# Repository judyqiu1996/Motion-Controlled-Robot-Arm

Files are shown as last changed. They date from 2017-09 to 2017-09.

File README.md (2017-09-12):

# Motion Controlled Robot Arm

1. Designed a circuit and PCB board receiving the sensor information from arm by Bluetooth and controlling the action of the robot.

2. Used I2C and SPI methods to communicate between chip and software.

3. Devised an algorithm of filtering and processing sensor data, manipulating robot arm in 3 Axis, including pitch and roll axes.

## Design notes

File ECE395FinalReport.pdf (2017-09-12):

# Motion Controlled Robotic Arm

# ECE 395 Spring 2017 Project

# Sanchit Anand & Yujia Qiu

# Introduction

For our project in ECE 395, we decided to make a motion controlled robotic arm that is capable of detecting the orientation of a person’s hand, and attempting to replicate the motion. Our project was based on another project from the Fall of 2013 - Human Controlled Robotic Arm and Legs Movement, and we attempted to extend the degrees of motion of the arm.

At the end of the project, major changes were made to the motion filtering algorithms, to support a new system of kinematics. This report is written in the hope that future students will be able to expand upon our work.

# Schematic

The schematic files we used include a different version of the LPC ARM processor, with almost identical functionality.

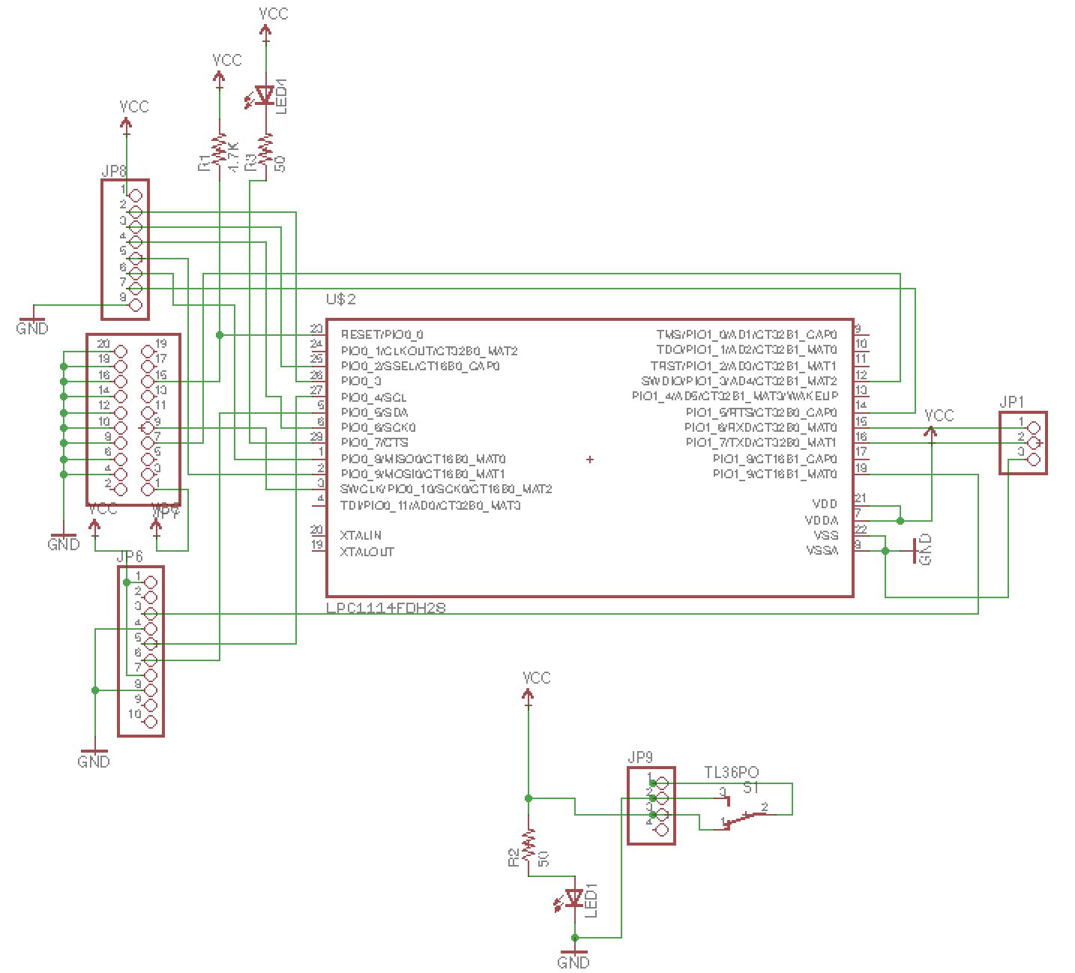
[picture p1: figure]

# Figure: Schematic Diagram

The 8 pins jumper is to connect the bluetooth breakout, the 10 pins jumper is to connect sensor breakout. The 20 pins jumper is to connect JTAG. The “JP1” is for switch which controls the power on or off. The “JP9” is connect to the power cell.

# PCB

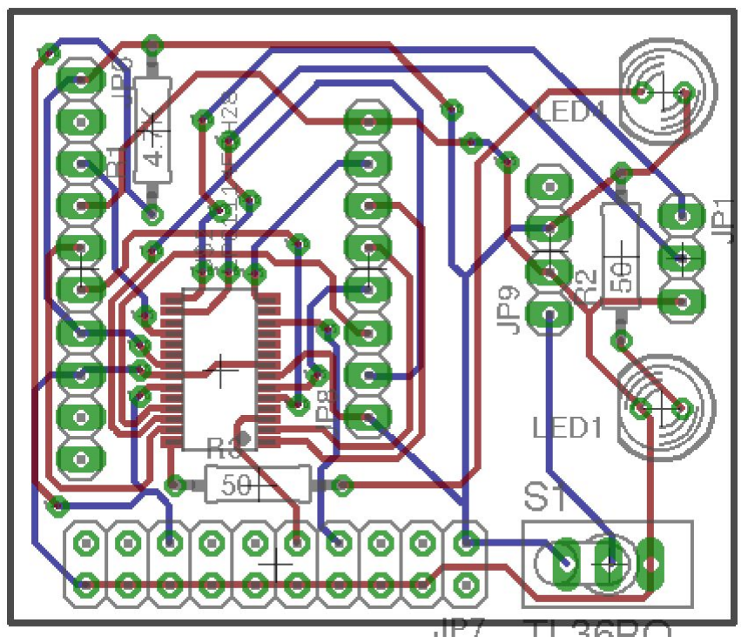
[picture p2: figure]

# Figure: PCB

# This brd file is transferred from schematic. And the figure below is the

actual picture of the pcb board.

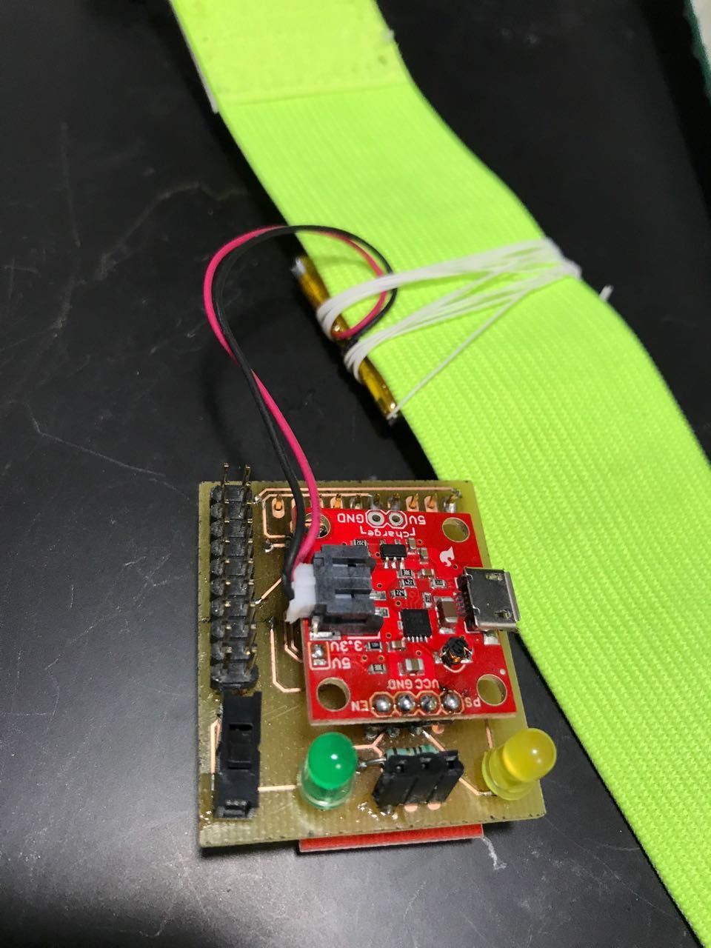
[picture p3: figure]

# Figure: pcb board picture

# Operation

The project hardware is split up between two different boards. There is a main prototype board

# that controls the motors, via USART protocol. This main board contains a bluetooth

module(NRF24l01+) that polls for data from the motion pads at regular intervals. This angular data is transformed into motor values, and transmitted via USART. There is an LED attached for debugging purposes, as well as connections for downloading code via JTAG module.

The motion pads consist of an battery pack, connected to a power chip that regulates voltage at 3.3V. It also contains a six axis IMU unit, the MPU-6050, for taking measurements of motion along the pitch and roll axes. The microprocessor performs complementary filtering on the data. Finally the bluetooth module (NRF24l01+), transmits the pitch and roll angles to the main board.

There are 4 motion pads in total, one for each shoulder joint, and one for each elbow joint. The 2 shoulder pads measure angles along pitch and roll axes, and transmit to the main board. Then the two separate motors in the shoulder joint get actuated by their respective angle. The 2 elbow pads measure motion along the pitch direction and transmit it to the main board, where the pitch angle from the shoulder joint is subtracted from it. The elbow motor is actuated by the resulting angle.

A short diagram is presented below to help understand the different angles used.

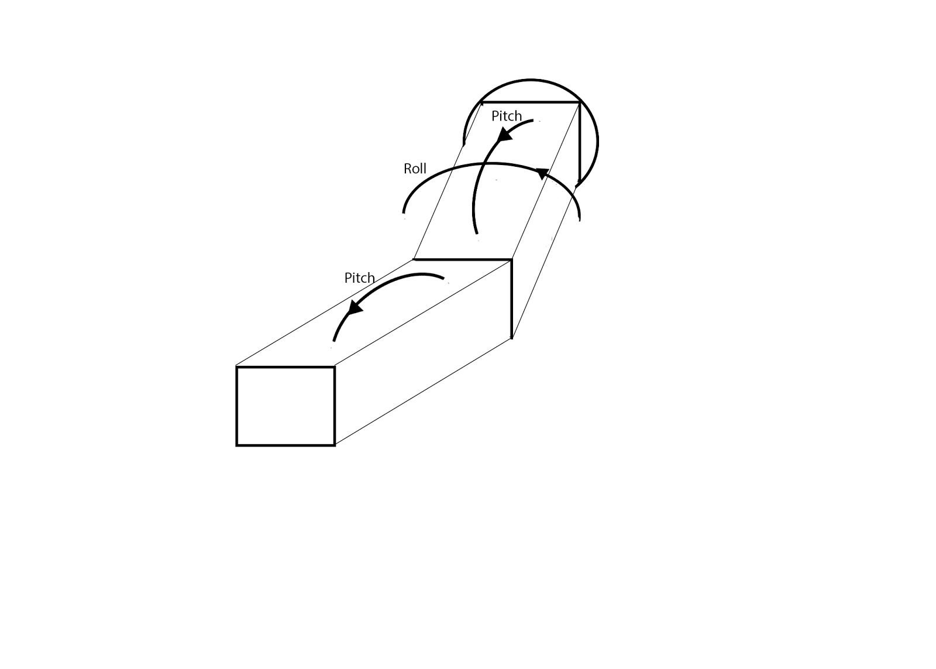
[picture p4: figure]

# Conclusion

The project yielded satisfactory results as determined by us. Lots of improvements can still be made on it. First of all, by using a 9 degree of freedom IMU, instead of a 6 degree of freedom IMU (The MPU-6050 used for this project), one would be able to measure all 3 axes of motion, instead of just two, and with a higher precision as well. One of the main limitations of using just 6 degrees of freedom is that the error in angles increases as the combined pitch and roll angles

# get higher. Secondly, by learning how to use the inbuild proprietary DMP software on the

MPU-6050, one would be able to offload all the filtering onto the IMU itself, and obtain much more accurate data in the process.

Finally, We found that the servos used in this project were liable to decreased performance after operating for some time. We are unsure whether it is the result of wear and tear, whether it is a fundamental property of the specific brand we used or an issue with the code being used. In either case, it is recommended that more research is done while selecting and using servos and motors to use in future projects.

# Appendix : Hardware

# NXP LPC1114 Cortex M0 Microprocessor (x5) The processors that perform all of the filtering and calculations, as well as

communications with various peripheral devices.

# http://www.nxp.com/documents/data_sheet/LPC111X.pdf

MPU6050 6-Axis Accelerometer/Gyroscope These are the main sensors. The inbuilt gyroscope and accelerometers measures the orientation of the board with respect to gravity. These measurements are stored in registers of the chip, and can be accessed by microprocessors via I2C protocol. The communication rate is 100Kbits/s. Documentation for this chip is available at http://www.invensense.com/mems/gyro/mpu6050.html

# NRF24L01+ Transceiver

This is a 2.4Ghz radio frequency transmitter/receiver. It is present on both the satellite and the main board, providing a form of wireless communication between the boards.

# The transceiver operates in two modes, one for receiving (RX) and one for transmission (TX). This can be configured by commands from the microprocessor through Serial

Peripheral Interface (SPI) protocol.

# http://www.nordicsemi.com/eng/Products/2.4GHz-RF/nRF24L01

Dynamixel AX-12a Servos The AX12 servos are the actuators of the robot, serving as rotational joints based on the commands sent by the microprocessor. These servos work on 9-12V power source and communicate with the microprocessor via a single line. The ID of the servos determines which servo along the series line to receive the instruction as passed from the

processor. The servos utilize half-duplex communication protocol.

# http://www.crustcrawler.com/products/bioloid/docs/AX-12.pdf

# Appendix : Code

complementary.c : C file containing the majority of filtering code.

#include "complementary.h"

float x_filter=0, y_filter=0, z_filter=0, angle_x=0, angle_y=0, angle_z=0 ;
float pitch , yaw, roll ;
float sign;
void complementary_filter(float * Buf,float accel_x, float accel_y, float accel_z, float gyro_x, float gyro_y, float gyro_z,float dt)
{

x_filter = 0.9*x_filter + 0.1*accel_x;
z_filter = 0.9*z_filter + 0.1*accel_z;
y_filter = 0.9*y_filter + 0.1*accel_y;
//acc_angle_y = atan2(x_filter, -z_filter) * 180/3.14159265358979323 ; //angle_y = 0.98*(gyro_y*dt + angle_y) + 0.02*acc_angle_y;

//acc_angle_x = atan2(y_filter, -z_filter) * 180/3.14159265358979323 ; //angle_x = 0.98*(gyro_x*dt + angle_x) + 0.02*acc_angle_x;

//acc_angle_z = atan2(x_filter,y_filter) * 180/3.14159265358979323 ; //angle_z = 0.98*(gyro_z*dt + angle_z) + 0.02*acc_angle_z;
angle_z = angle_z + gyro_z * dt;
sign = z_filter > 0?-1:1;
pitch = atan2(-x_filter,sqrt(y_filter*y_filter + z_filter*z_filter)) * 180/3.14159265358979323 ; roll = atan2(y_filter, sign* sqrt(z_filter*z_filter + 0.01*x_filter*x_filter))* 180/3.14159265358979323; angle_x = 0.98*(gyro_x*dt + angle_x) + 0.02*roll;
angle_y = 0.98*(gyro_y*dt + angle_y) + 0.02*pitch;
Buf[0] = angle_x;
Buf[1] = angle_y;
//Buf[2] = angle_z;
}

# main.c : Code that handles the major initialization and communication (Only including

some of the code for brevity).

#define TRANSMITTER 0x0

#define RECEIVER 0x1

#define SET_ID | 0x2

/*** CHOOSE BOARD ***/
/********************/

//#define BOARD TRANSMITTER #define BOARD RECEIVER
//#define BOARD SET_ID
/********************/

int main(void) {

delay32Ms(1, 2000);//allow time for devices to power up LED_DIR_OUT;
LPC_GPIO1->DIR &= ~(1<<5); //input mode
SER_init();
Led_Blink();

//initialize SPI protocol
SSP_IOConfig(0);
SSP_Init(0);

Led_Blink();

#if BOARD == TRANSMITTER

AX12_begin(_1MHZ);
NRF24L01_Init(_RX_MODE, _CH1, _1Mbps, Address, _Address_Width, _Buffer_Size); while(1)
{

NRF24L01_Set_TX_Address(Address, _Address_Width); NRF24L01_Set_RX_Pipe(0, Address, _Address_Width, _Buffer_Size);

for(i=0; i < _Buffer_Size; i++) Buf[i] = '\0'; strcpy(Buf,"HELLO\0");
//Transmit Request
NRF24L01_Send(Buf);
delay32Ms(1,5);
//Receive Response
NRF24L01_Receive(Buf);

value = (float*) Buf;

if(value[1] == 0.0 ) {}
else{
temp = value[1];
if(temp <-60) temp = -60;
if(temp > 60) temp = 60;
//value[1] = value[1];
temp = (150 + temp)*1023/300; i = temp;
//printf("%d,",i);
AX12_move(14,i);

}
delay32Ms(1,1);

if(value[0] == 0.0) {}

else{
pitch = value[0];
temp = value[0];
if(temp <-90) temp = -90;
if(temp > 90) temp = 90;
//value[1] = value[1] - 30; temp = ( 150 + temp )*1023/300; i = temp;
AX12_move(15,i);
}

}
#endif

#if BOARD == RECEIVER

NRF24L01_Init(_RX_MODE, _CH1, _1Mbps, Address3, _Address_Width, _Buffer_Size); NRF24L01_DRint_Init();
I2CInit(I2CMASTER);

while(MPU6050_init() != 0) {
for(i=0;i<100000;i++);
}

delay32Ms(1,500);
MPU6050_setZero();
init_timer32(0, 48); //us
enable_timer32(0);
while(1)
{

gyroy = MPU6050_getGyroRoll_degree(); gyrox = MPU6050_getGyroX();
gyroz = MPU6050_getGyroZ();
dt = (float)read_timer32(0) / 1000000;

//printf("%f\r\n",gyroz);
//gyro = gyro;
reset_timer32(0);
enable_timer32(0);
x = MPU6050_getAccel_x();
z = MPU6050_getAccel_z();
y = MPU6050_getAccel_y();
complementary_filter(list,x,y,z,gyrox,gyroy, gyroz, dt); cvalue = (char*) list;
//Receive Response
if(LPC_GPIO1->MASKED_ACCESS[1<<5] == 0)
{
//NRF24L01_Print_Register(); NRF24L01_Receive(Buf);
if(strncmp(Buf,"HELLO",_Buffer_Size)==0) {
memset(Buf,0,_Buffer_Size); for(i=0;i<sizeof(float)*2;i++) Buf[i] = cvalue[i]

NRF24L01_Send(Buf);
}
}
}

#endif

#if BOARD == SET_ID

AX12_begin(_1MHZ);
AX12_setID(BROADCAST_ID, ID);
LED_ON;
AX12_ledStatus(ID, ON); | //Check if loaded
AX12_move(ID, 512);
#endif

}

mpu6050.c: added more functions on top of existing class.

void MPU6050_setZero(){

uint16_t i;
uint16_t n = 1000;
int32_t tmp_y= 0,tmp_x = 0, tmp_z = 0; int32_t ac_x=0, ac_y = 0, ac_z = 0;

for(i=0;i<n;i++){
tmp_y += MPU6050_getGyroRoll_raw(); }
for (i=0;i<n;i++){
tmp_z += MPU6050_getGyroZ_raw();
}
for(i=0;i<n;i++){

tmp_x += MPU6050_getGyroX_raw(); }
for (i=0;i<n;i++){
ac_x += MPU6050_getAccel_x_raw(); }
for (i=0;i<n;i++){
ac_y += MPU6050_getAccel_y_raw(); }
for (i=0;i<n;i++){
ac_z += MPU6050_getAccel_z_raw(); }
tmp_y /= n;
tmp_x /= n;
tmp_z /= n;
ac_y /= n;
ac_x /= n;
ac_z /= n;
zero_gyro_roll = tmp_y;
zero_X = tmp_x;
zero_Z = tmp_z;
zero_acc_x = ac_x;
zero_acc_z = ac_z + 2048;
zero_acc_y = ac_y;

}

int16_t MPU6050_getAccel_y_raw(){

int16_t tmp;
uint8_t state;
I2CWriteLength | | = 2;
I2CReadLength | = 2; | //1;
I2CMasterBuffer[0] | | = MPU6050_ADDRESS;
I2CMasterBuffer[1] | | = MPU6050_RA_ACCEL_YOUT_H;
I2CMasterBuffer[2] | | = MPU6050_ADDRESS | RD_BIT;

state = I2CEngine();
if(state != I2C_OK) return 1;
tmp = (I2CSlaveBuffer[0] << 8) | I2CSlaveBuffer[1];

return tmp - zero_acc_y;
}

float MPU6050_getAccel_y(){

int16_t tmp;
float y;
tmp = MPU6050_getAccel_y_raw(); y = (float) tmp/2048;
return y;

}

int16_t MPU6050_getGyroX_raw(void)

{
int16_t tmp;
uint8_t state;
I2CWriteLength | = 2;
I2CReadLength | = 2; //1;
I2CMasterBuffer[0] | = MPU6050_ADDRESS;
I2CMasterBuffer[1] | = MPU6050_RA_GYRO_XOUT_H;
I2CMasterBuffer[2] | = MPU6050_ADDRESS | RD_BIT;

state = I2CEngine();
if(state != I2C_OK) return 1;
tmp = (I2CSlaveBuffer[0]<<8) | I2CSlaveBuffer[1];

return tmp - zero_X;

}
float MPU6050_getGyroX(void) {
int16_t tmp;
float roll;

tmp = MPU6050_getGyroX_raw(); roll = (tmp / 65.536 );
return roll;
}

int16_t MPU6050_getGyroZ_raw(void) {
int16_t tmp;
uint8_t state;
I2CWriteLength | = 2;
I2CReadLength | = 2; //1;
I2CMasterBuffer[0] | = MPU6050_ADDRESS;
I2CMasterBuffer[1] | = MPU6050_RA_GYRO_ZOUT_H;
I2CMasterBuffer[2] | = MPU6050_ADDRESS | RD_BIT;

state = I2CEngine();
if(state != I2C_OK) return 1;
tmp = (I2CSlaveBuffer[0]<<8) | I2CSlaveBuffer[1];

return tmp - zero_Z;

}

float MPU6050_getGyroZ(void) {
int16_t tmp;
float roll;

tmp = MPU6050_getGyroZ_raw(); roll = (tmp / 65.536 );
return roll;
}

# nrf24l01.c: added one function on top of existing class

void NRF24L01_Init_Auto_Ack(char Device_Mode, char CH, char DataRate, char *Address, char Address_Width, char Size_Payload) {

NRF24L01_CE_OUT; // Set Port DIR out

// Disable Enhanced ShockBurst
NRF24L01_WriteReg(W_REGISTER | EN_AA, 0x1);
NRF24L01_WriteReg(W_REGISTER | SETUP_RETR, 0x1);
// RF output power in TX mode = 0dBm (Max.)
// Set LNA gain
NRF24L01_WriteReg(W_REGISTER | RF_SETUP, 0x07 | DataRate); //0b00000111 | DataRate);

NRF24L01_Set_Address_Width(Address_Width);

NRF24L01_Set_RX_Pipe(0, Address, Address_Width, 0); NRF24L01_Set_RX_Pipe(1, Address, Address_Width, Size_Payload); NRF24L01_Set_CH(CH);

NRF24L01_Set_TX_Address(Address, Address_Width); // Set Transmit address

// Bits 4..6: Reflect interrupts as active low on the IRQ pin
// Bit 3: Enable CRC
// Bit 2: CRC 1 Byte
// Bit 1: Power Up
NRF24L01_WriteReg(W_REGISTER | CONFIG, 0x0A | Device_Mode);//0b00001010 | Device_Mode);

delay32Us(1, 1500);
if(Device_Mode == _RX_MODE) //take it out of standby
{ NRF24L01_CE_HIGH; delay32Us(1, 130);

}
//Delay_us(1500);
}

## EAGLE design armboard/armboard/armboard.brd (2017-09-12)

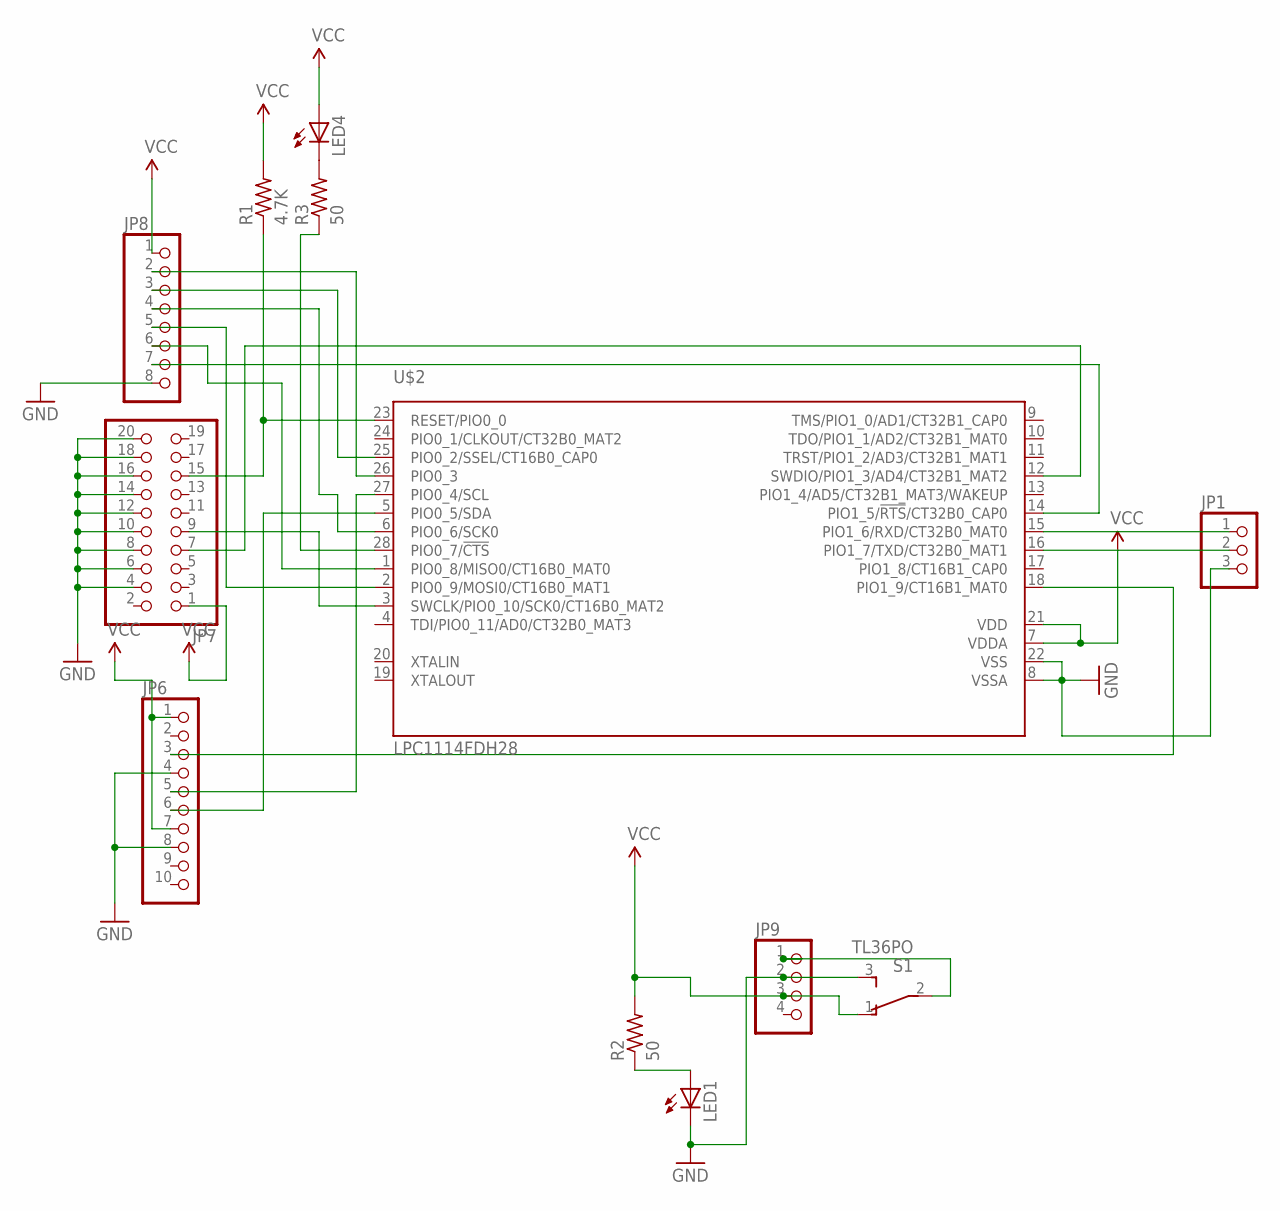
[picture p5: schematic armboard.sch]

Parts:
JP1: PINHD-1X3; 1X03
JP6: PINHD-1X10; 1X10
JP7: PINHD-2X10; 2X10
JP8: PINHD-1X8; 1X08
JP9: PINHD-1X4; 1X04
LED1, LED4: LED5MM
R1: 4.7K; 0207/10
R2, R3: 50; 0207/10
S1: TL36PO; TL3XPO
U$2: LPC1114FDH28; SOT361-1

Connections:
GND: JP1.3, JP6.4, JP6.8, JP7.4, JP7.6, JP7.8, JP7.10, JP7.12, JP7.14, JP7.16, JP7.18, JP7.20, JP8.8, JP9.2, LED1.K (C), S1.3 (S), U$2.8 (VSSA), U$2.22 (VSS)
unnamed: JP7.15, R1.1, U$2.23 (RESET/PIO0_0)
unnamed: JP9.1, S1.2
unnamed: LED4.K (C), R3.2
unnamed: R3.1, U$2.28 (PIO0_7/!CTS!)
unnamed: JP7.9, U$2.3 (SWCLK/PIO0_10/SCK0/CT16B0_MAT2)
unnamed: JP8.6, U$2.1 (PIO0_8/MISO0/CT16B0_MAT0)
unnamed: JP1.1, U$2.15 (PIO1_6/RXD/CT32B0_MAT0)
unnamed: JP8.5, U$2.2 (PIO0_9/MOSI0/CT16B0_MAT1)
unnamed: JP8.3, U$2.25 (PIO0_2/SSEL/CT16B0_CAP0)
unnamed: JP6.6, U$2.5 (PIO0_5/SDA)
unnamed: JP8.2, U$2.26 (PIO0_3)
unnamed: JP1.2, U$2.16 (PIO1_7/TXD/CT32B0_MAT1)
unnamed: JP6.3, U$2.18 (PIO1_9/CT16B1_MAT0)
unnamed: JP8.4, U$2.6 (PIO0_6/SCK0)
unnamed: LED1.A, R2.1
unnamed: JP8.7, U$2.14 (PIO1_5/!RTS!/CT32B0_CAP0)
unnamed: JP6.5, U$2.27 (PIO0_4/SCL)
unnamed: JP7.7, U$2.12 (SWDIO/PIO1_3/AD4/CT32B1_MAT2)
VCC: JP6.1, JP6.7, JP7.1, JP8.1, JP9.3, LED4.A, R1.2, R2.2, S1.1 (O), U$2.7 (VDDA), U$2.21 (VDD)

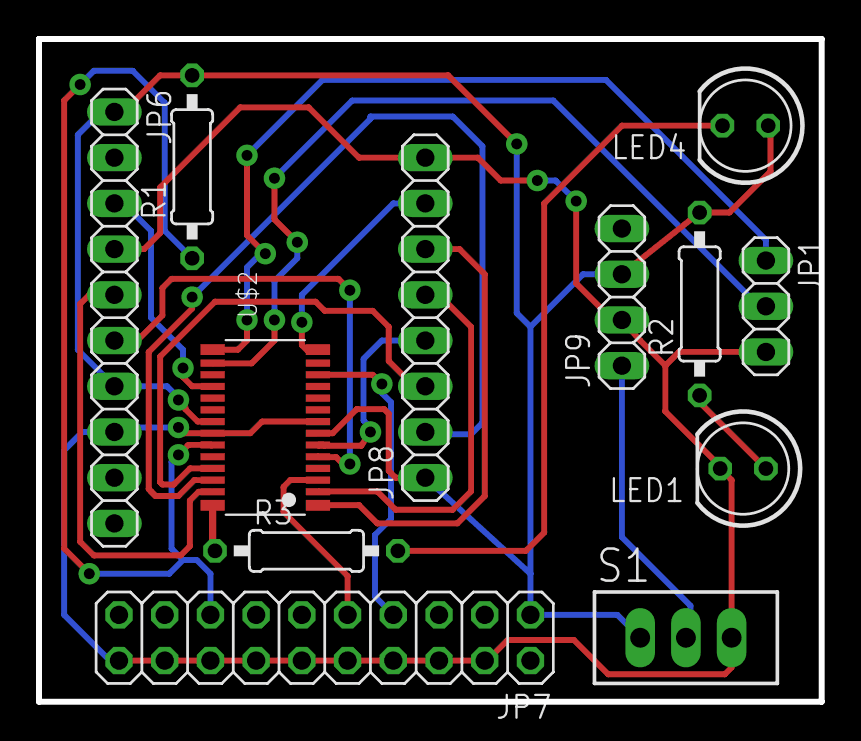
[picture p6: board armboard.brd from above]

Board: 2 copper layers, 43.5 x 36.8 mm, 12 parts (0 on the bottom side), 20 nets.

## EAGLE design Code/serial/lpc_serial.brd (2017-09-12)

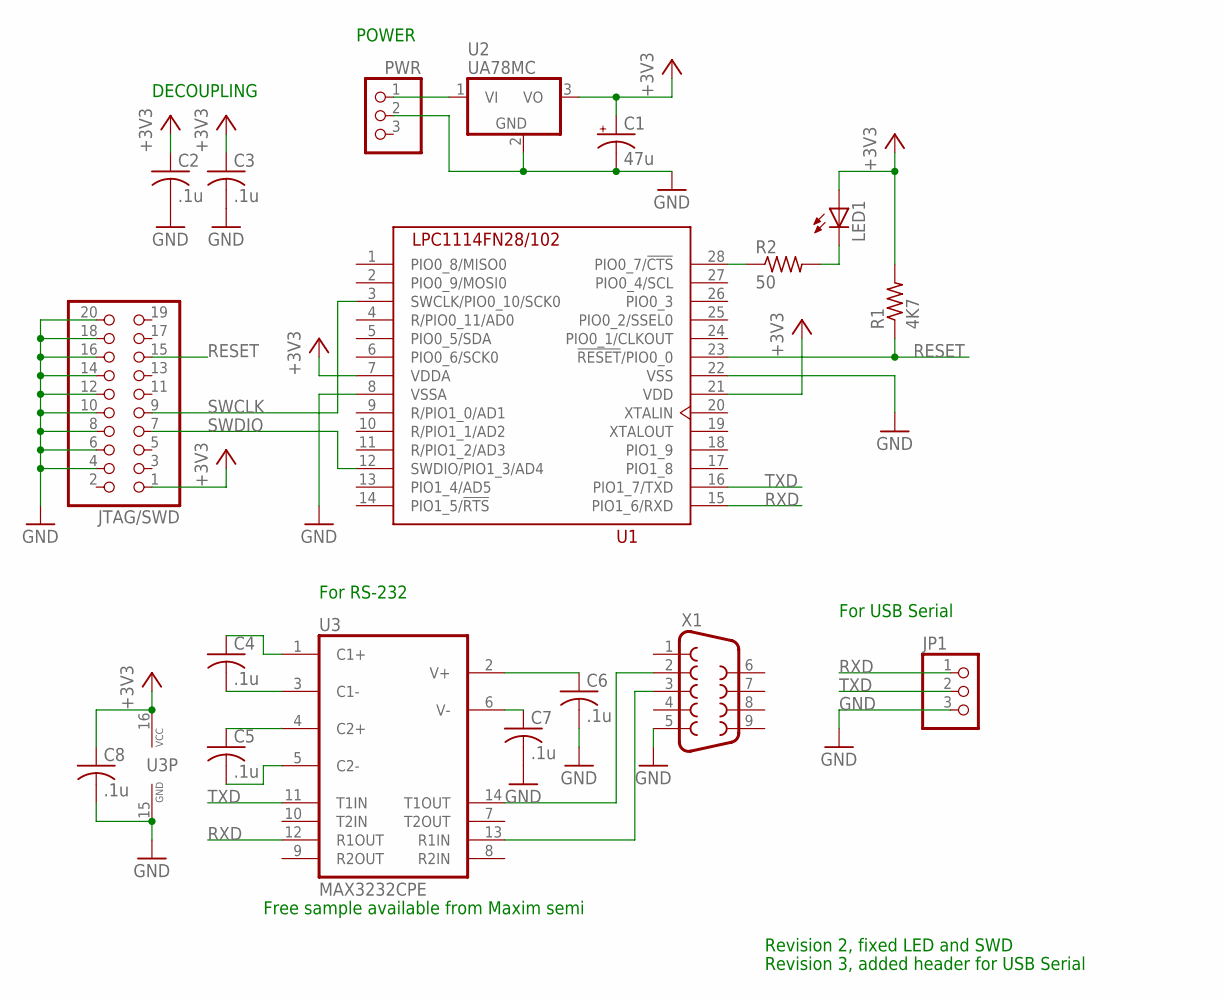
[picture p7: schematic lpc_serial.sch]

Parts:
C1: 47u; E3,5-8
C2, C3, C4, C5, C6, C7, C8: .1u; C050-024X044
JP1: PINHD-1X3; 1X03
JTAG/SWD: PINHD-2X10; 2X10
LED1: LED10MM
PWR: PINHD-1X3; 1X03
R1: 4K7; 0207/10
R2: 50; 0207/10
U1: LPC1114FN28/102; DIL28-6
U2: UA78MC; TO220V
U3: MAX3232CPE; DIL16
X1: F09H

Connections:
+3V3: C1.+, C2.1, C3.1, C8.1, JTAG/SWD.1, LED1.A, R1.2, U1.7 (VDDA), U1.21 (VDD), U2.3 (VO), U3.16 (VCC)
GND: C1.-, C2.2, C3.2, C6.2, C7.2, C8.2, JP1.3, JTAG/SWD.4, JTAG/SWD.6, JTAG/SWD.8, JTAG/SWD.10, JTAG/SWD.12, JTAG/SWD.14, JTAG/SWD.16, JTAG/SWD.18, JTAG/SWD.20, PWR.2, U1.8 (VSSA), U1.22 (VSS), U2.2 (GND), U3.15 (GND), X1.5
unnamed: LED1.K (C), R2.2
unnamed: PWR.1, U2.1 (VI)
unnamed: R2.1, U1.28 (PIO0_7/!CTS)
unnamed: U3.14 (T1OUT), X1.2
unnamed: U3.13 (R1IN), X1.3
unnamed: C4.1, U3.1 (C1+)
unnamed: C4.2, U3.3 (C1-)
unnamed: C5.1, U3.4 (C2+)
unnamed: C5.2, U3.5 (C2-)
unnamed: C6.1, U3.2 (V+)
unnamed: C7.1, U3.6 (V-)
RESET: JTAG/SWD.15, R1.1, U1.23 (!RESET!/PIO0_0)
RXD: JP1.1, U1.15 (PIO1_6/RXD), U3.12 (R1OUT)
SWCLK: JTAG/SWD.9, U1.3 (SWCLK/PIO0_10/SCK0)
SWDIO: JTAG/SWD.7, U1.12 (SWDIO/PIO1_3/AD4)
TXD: JP1.2, U1.16 (PIO1_7/TXD), U3.11 (T1IN)

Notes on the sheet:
POWER
DECOUPLING
Revision 2, fixed LED and SWD
Free sample available from Maxim semi
For USB Serial
For RS-232
Revision 3, added header for USB Serial

Board: 2 copper layers, 18 parts (0 on the bottom side), 18 nets, no tracks yet.

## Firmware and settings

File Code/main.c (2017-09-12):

/*
 * TELE_ROBO_MIMCRY 
 * 
 * ECE 395
 * Spring 2013
 * 
 * Matthew Johnson
 * Eric Badger
 */

#include "driver_config.h"

#include "ssp.h"
#include "cpu_lpc1000.h"
#include "nrf24l01.h"
#include "uart.h"
#include "mpu6050.h"
#include "kalman.h"
#include "complementary.h"
#include "i2c.h"
#include "timer32.h"
#include <math.h>
#include "AX12.h"
#include <stdio.h>
#include <stdlib.h>
#include <rt_misc.h>
#include <string.h>	 
//#include "LPC11xx.h"

#define TRANSMITTER 0x0
#define RECEIVER 0x1
#define SET_ID		0x2


/*** CHOOSE BOARD ***/
/********************/

//#define BOARD TRANSMITTER
#define BOARD RECEIVER
//#define BOARD SET_ID
/********************/

// Channel 0..125
#define	_CH1 5  //robot 1's frequency		    
#define _CH2 16	//robot 2's frequency
#define	_Address_Width	5	// 3..5
#define _Buffer_Size 32    // 1..32

//LED Functions
#define LED_DIR_OUT LPC_GPIO0->DIR |= (1<<7);
#define LED_ON LPC_GPIO0->MASKED_ACCESS[(1<<7)] = 0
#define LED_OFF  LPC_GPIO0->MASKED_ACCESS[(1<<7)] = (1<<7)	


/*----------------------------------------------------------------------------
  Initialize UART pins, Baudrate
 *----------------------------------------------------------------------------*/
void SER_init (void) {
   
  /* configure PINs GPIO1.6, GPIO1.7 for UART */
  LPC_SYSCON->SYSAHBCLKCTRL |= ((1UL <<  6) |   /* enable clock for GPIO      */
                                (1UL << 16) );  /* enable clock for IOCON     */

  LPC_IOCON->PIO1_6  =  (1UL <<  0);            /* P1.6 is RxD                */
  LPC_IOCON->PIO1_7  =  (1UL <<  0);            /* P1.7 is TxD                */

  /* configure UART0 */
  LPC_SYSCON->SYSAHBCLKCTRL |=  (1UL << 12);    /* Enable clock to UART       */
  LPC_SYSCON->UARTCLKDIV     =  (4UL <<  0);    /* UART clock =  CCLK / 4     */

  LPC_UART->LCR = 0x83;                   /* 8 bits, no Parity, 1 Stop bit    */
  LPC_UART->DLL = 4;                      /* 115200 Baud Rate @ 12.0 MHZ PCLK */
  LPC_UART->FDR = 0x85;                   /* FR 1.627, DIVADDVAL 5, MULVAL 8  */
  LPC_UART->DLM = 0;                      /* High divisor latch = 0           */
  LPC_UART->LCR = 0x03;                   /* DLAB = 0                         */
}




/* Import external functions from Serial.c file                               */
//extern void SER_init (void);

void Led_Blink(void) {
 	LED_ON;
	delay32Ms(1, 1000);
	LED_OFF;
	delay32Ms(1, 500);

}

//Globals for interrupt from nRF24L01+
volatile uint8_t MPU_Request = 0;
char Buf[_Buffer_Size] = {'\0'}; 

void NRF24L01_Print_Register()
{
	uint32_t i;
	uint32_t j = 0;
	for(i=0;i<24;i++)
	{
		if (j <5)
		{
			printf("%d:0x%x ",i,NRF24L01_ReadReg(i));
			j++;
		}
		
		else
		{
			printf("%d:0x%x ",i,NRF24L01_ReadReg(i));
			printf("\r\n");
			j=0;
		}
	}
	printf("\r\n");
}


NRF24L01_Print_R(char Reg, int Size)
{
	char Buf[10];
	int i;
	NRF24L01_ReadRegBuf(Reg, Buf, Size);
	printf("%d: ",Reg );
	for (i=0;i<Size;i++)
		printf("%x ",Buf[i]);
	printf("\r\n");
	
}
//Reads from RX FIFO, blocks until success or timeout
void NRF24L01_Receive(char Buf[_Buffer_Size]) {
	uint32_t i = 0;
	uint32_t j = 0;

	while ((NRF24L01_Get_Status() & _RX_DR) != _RX_DR && i < 0xFF) i++;
	if(i >= 0xFF)
	{
		NRF24L01_WriteReg(W_REGISTER | STATUS, _RX_DR );
		for(j=0; j < _Buffer_Size; j++) Buf[j] = '\0';
		return;
	}

	NRF24L01_CE_LOW;

	NRF24L01_Read_RX_Buf(Buf, _Buffer_Size);
	NRF24L01_WriteReg(W_REGISTER | STATUS, _RX_DR );
}

//Transmits data, blocks until success or timeout
void NRF24L01_Send(char Buf[_Buffer_Size]) {
	uint32_t i = 0;
	NRF24L01_Set_Device_Mode(_TX_MODE);
	NRF24L01_Write_TX_Buf(Buf, _Buffer_Size);															    
	while(i == 0)
	{
	NRF24L01_RF_TX();
	//delay32Ms(1,1);
	while ((NRF24L01_Get_Status() & _TX_DS)!= _TX_DS && (NRF24L01_Get_Status() & _MAX_RT)!= _MAX_RT);
	if ((NRF24L01_Get_Status() & _MAX_RT) != _MAX_RT)i = 1;
	NRF24L01_WriteReg(W_REGISTER | STATUS, _TX_DS | _MAX_RT);
	}
	NRF24L01_Set_Device_Mode(_RX_MODE);
}

int main(void) {
	

//BASE STATION MASTER_ARM
int32_t i=0;
	int ID = 11;
	float gyrox,gyroy,gyroz,y,x,z,dt;
	float temp;
	float pitch,pitch2;
	float * value;
	char * cvalue;
	float list[4];
	//int position[] = {511, 511, 511, 511, 511, 511};
//	uint8_t robot1_2;
	//uint16_t CH;
	char Address[_Address_Width] = { 0x11, 0x22, 0x33, 0x44, 0x55 };
	char Address2[_Address_Width] = {0x11, 0x21, 0x33, 0x44, 0x55};
	char Address3[_Address_Width] = {0x11, 0x23, 0x33, 0x44, 0x55};
	//char * sensor[] = {"R_ROTATOR", "R_SHOULDER", "R_ELBOW", "L_ROTATOR", "L_SHOULDER", "L_ELBOW"};

	
	delay32Ms(1, 2000);//allow time for devices to power up
	LED_DIR_OUT;
	LPC_GPIO1->DIR &= ~(1<<5); //input mode	
	SER_init();	
	Led_Blink();
	
/*
	//initialize serial, also initializes GPIO
	AX12_begin(_1MHZ);
	LED_DIR_OUT;		 

	//toggle servo status LEDs
	AX12_ledStatus(BROADCAST_ID, ON);
	delay32Ms(1,1000);
	AX12_ledStatus(BROADCAST_ID, OFF);

	//initialize servos to 180 degrees
	for(i=0; i < 6; i++)
	{
		 AX12_move(i, position[i]);
		 delay32Ms(1, 500);
	}
*/
	
	//initialize SPI protocol
	SSP_IOConfig(0);
	SSP_Init(0); 
	
	Led_Blink();
/*	
	//Read Robot Switch
	robot1_2 =  LPC_GPIO1->MASKED_ACCESS[(1<<2)];
	if(robot1_2) CH = _CH1;
	else CH = _CH2;
*/

	//Initialize transceiver		
	
	
	Led_Blink();
#if BOARD == TRANSMITTER
	AX12_begin(_1MHZ);
	NRF24L01_Init(_RX_MODE, _CH1, _1Mbps, Address, _Address_Width, _Buffer_Size);
		//init_timer32(0, 48); //us
	//enable_timer32(0);
	while(1)
	{
		//AX12_move(BROADCAST_ID,512);
			//delay32Ms(1,5);
		//printf("Starting\r\n");
		
		
	
			
		
		
		
		
			NRF24L01_Set_TX_Address(Address, _Address_Width);
			NRF24L01_Set_RX_Pipe(0, Address, _Address_Width, _Buffer_Size);
		
			
			//Address[2] = i;
			//Switch Address
			//NRF24L01_Set_TX_Address(Address, _Address_Width);
			//NRF24L01_Set_RX_Pipe(0, Address, _Address_Width, _Buffer_Size);
			//Clear and Initiialize Buffer
			for(i=0; i < _Buffer_Size; i++) Buf[i] = '\0'; 
				strcpy(Buf,"HELLO\0");
			//Transmit Request	   		
			NRF24L01_Send(Buf);	
			delay32Ms(1,5);
			//Receive Response
			//NRF24L01_Print_Register();
			//NRF24L01_Print_R(0xA,5);
			//NRF24L01_Print_R(0x10,5);
			NRF24L01_Receive(Buf);
			
			//printf("%d				%d\r\n",i,k);
			value = (float*) Buf;
			//printf("%f ",value[0]);
			//printf("%f\r\n",value[1]);
			//if(i==0){i=1;angle=180;}
			//else{angle =(angle + value[1]) ;}
			
			
			
			//if(value[0] == 0.0 || value[2] ==0.0 )continue;
		
			//printf("1:%.2f,%.2f\r\n",value[0],value[1]);
			
			if(value[1] == 0.0 ) {}
			else{
			temp = value[1];
			if(temp <-60) temp = -60;
			if(temp > 60) temp = 60;
			//value[1] = value[1];
			temp = (150 + temp)*1023/300;
			i = temp;
			//printf("%d,",i);
			AX12_move(14,i);
				
			}
			delay32Ms(1,1);
			
			if(value[0] == 0.0) {}
			
			else{
			pitch = value[0];
			//value[1] = (value[1]>0)?value[1]:  360+(value[1]);
			//value[1] = 360.0-value[1];
				temp = value[0];
			if(temp <-90) temp = -90;
			if(temp > 90) temp = 90;
			//value[1] = value[1] - 30;
			temp = ( 150 +  temp )*1023/300;
			i = temp;
			AX12_move(15,i);
			//printf("%d,",i);
			}
			
		
			//delay32Ms(1,2);
			//printf("%d\r\n",l);
			
			//printf("%d\n",i);
			//delay32Ms(1,20);
			//printf("%f\r\n",*value);
		
				NRF24L01_Set_TX_Address(Address2, _Address_Width);
				NRF24L01_Set_RX_Pipe(0, Address2, _Address_Width, _Buffer_Size);
				
				
				for(i=0; i < _Buffer_Size; i++) Buf[i] = '\0'; 
				strcpy(Buf,"HELLO\0");
			//Transmit Request	   		
				NRF24L01_Send(Buf);	
				delay32Ms(1,5);
			//Receive Response
				//NRF24L01_Print_Register();
			//	NRF24L01_Print_R(0xA,5);
				//NRF24L01_Print_R(0x10,5);
				NRF24L01_Receive(Buf);
			
				value = (float*) Buf;
				//printf("2:%.2f\r\n",value[0]);
				if(value[0] == 0.0 ) {}
				else{
				temp = value[0] - pitch;
				//value[1] = (value[1]>0)?value[1]:  360+(value[1]);
				//value[1] = 360.0-value[1];
				if(temp <0) temp = 0;
				if(temp > 90) temp = 90;
				//value[1] = value[1] - 30;
				temp = ( 150 -  temp )*1023/300;
				i = temp;
				AX12_move(16,i);
				//printf("%d\r\n",i);
				
					} 
				
					//delay32Ms(1,1000);
					
					
						NRF24L01_Set_TX_Address(Address3, _Address_Width);
				NRF24L01_Set_RX_Pipe(0, Address3, _Address_Width, _Buffer_Size);
				
				
				for(i=0; i < _Buffer_Size; i++) Buf[i] = '\0'; 
				strcpy(Buf,"HELLO\0");
			//Transmit Request	   		
				NRF24L01_Send(Buf);	
				delay32Ms(1,5);
			//Receive Response
				//NRF24L01_Print_Register();
			//	NRF24L01_Print_R(0xA,5);
				//NRF24L01_Print_R(0x10,5);
				NRF24L01_Receive(Buf);

				value = (float*) Buf;
					
				if(value[1] == 0.0 ) {}
				else{
				temp = value[1];
				if(temp <-60) temp = -60;
				if(temp > 60) temp = 60;
				//value[1] = value[1];
				temp = (150 + temp)*1023/300;
				i = temp;
				//printf("%d,",i);
				AX12_move(12,i);
				
			}
			delay32Ms(1,1);
			
			if(value[0] == 0.0) {}
			
			else{
			pitch2 = value[0];
			//value[1] = (value[1]>0)?value[1]:  360+(value[1]);
			//value[1] = 360.0-value[1];
				temp = value[0];
			if(temp <-90) temp = -90;
			if(temp > 90) temp = 90;
			//value[1] = value[1] - 30;
			temp = ( 150 -  temp )*1023/300;
			i = temp;
			AX12_move(13,i);
			//printf("%d,",i);
			}
			//delay32Ms(1,1);
			//AX12_move(11,65);
				
		}
#endif	
		
#if BOARD == RECEIVER			
	NRF24L01_Init(_RX_MODE, _CH1, _1Mbps, Address3, _Address_Width, _Buffer_Size);
	NRF24L01_DRint_Init();
	I2CInit(I2CMASTER);
  //MPU6050_initialize();
//	MPU6050_dmp_init();
//	printf("All done!!\r\n");
		
		
		
			while(MPU6050_init() != 0)
	{
		for(i=0;i<100000;i++);
	} 
	
	
		delay32Ms(1,500);
	MPU6050_setZero();
	//kalman_init();
	init_timer32(0, 48); //us
	enable_timer32(0);
	while(1)
	{
	
		
		
		gyroy =  MPU6050_getGyroRoll_degree();
		gyrox =  MPU6050_getGyroX();
		gyroz = MPU6050_getGyroZ();
		dt = (float)read_timer32(0) / 1000000;
		
		//printf("%f\r\n",gyroz);
		//gyro = gyro;
		reset_timer32(0);
		enable_timer32(0);	
		x = MPU6050_getAccel_x();
		z = MPU6050_getAccel_z();
		y = MPU6050_getAccel_y();
		
		
		
		
		
		complementary_filter(list,x,y,z,gyrox,gyroy, gyroz, dt);
		
			//angle = kalman_update(acc_angle, gyro, dt);
			//angle = 0.1*acc_angle + 0.1*j + 0.1*k + 0.7*(gyro*dt + angle);
		//angle = 0.5*acc_angle + 0.5*(gyro*dt - l);
	
		//angle = 0.98*(gyro*dt + angle) + 0.02 * acc_angle;
			cvalue = (char*) list;
			//Receive Response
			if(LPC_GPIO1->MASKED_ACCESS[1<<5] == 0)
			{
			//NRF24L01_Print_Register();
			NRF24L01_Receive(Buf);
			if(strncmp(Buf,"HELLO",_Buffer_Size)==0)
			{
				memset(Buf,0,_Buffer_Size);
				for(i=0;i<sizeof(float)*2;i++)
					Buf[i] = cvalue[i];
				NRF24L01_Send(Buf);
			}
			



			
		}
		
		
		}
			
			
		

	
	
		
		
#endif
#if BOARD == SET_ID
	

	//BASE STATION MASTER FOR SETTING ID
	AX12_begin(_1MHZ);


	AX12_setID(BROADCAST_ID, ID);

	LED_ON;

	AX12_ledStatus(ID, ON);	  //Check if loaded
	AX12_move(ID, 512);
	
#endif
	
	}


//------------------------------------------------------------------------------------------

//--------------------------------------------------------------------------------

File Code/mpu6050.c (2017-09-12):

#include "mpu6050.h"


#include "i2c.h"

extern volatile uint8_t 	I2CMasterBuffer[BUFSIZE], I2CSlaveBuffer[BUFSIZE];
extern volatile uint32_t 	I2CReadLength, I2CWriteLength;

int16_t zero_acc_x = 0,zero_acc_z = 0 ,zero_acc_y=0;
int16_t zero_gyro_roll = 0, zero_X = 0, zero_Z = 0;

void clearBuffer()
{
	int i;
	for(i=0; i < BUFSIZE; i++) I2CMasterBuffer[i] = 0;
}

uint8_t MPU6050_init() {

	uint8_t state;
	
	clearBuffer();
	
	I2CWriteLength 		= 3;
	I2CReadLength		= 0;
	I2CMasterBuffer[0] 	= MPU6050_ADDRESS;
	I2CMasterBuffer[1] 	= MPU6050_RA_PWR_MGMT_1;
	I2CMasterBuffer[2] 	= 0x01; // reset device y-axis gyro as clk;

	state = I2CEngine();
	if(state != I2C_OK) return 1;


	I2CWriteLength 		= 3;
	I2CReadLength		= 0;
	I2CMasterBuffer[0] 	= MPU6050_ADDRESS;
	I2CMasterBuffer[1] 	= MPU6050_RA_CONFIG;
	I2CMasterBuffer[2] 	= 0x00; // Lowpass
	//I2CMasterBuffer[2] 	= 0b00000011; // Lowpass
	state = I2CEngine();
	if(state != I2C_OK) return 1;


	I2CWriteLength 		= 3;
	I2CReadLength		= 0;
	I2CMasterBuffer[0] 	= MPU6050_ADDRESS;
	I2CMasterBuffer[1] 	= MPU6050_RA_PWR_MGMT_1;
	I2CMasterBuffer[2] 	= 0x04; // wakeup

	state = I2CEngine();
	if(state != I2C_OK) return 1;


	I2CWriteLength 		= 3;
	I2CReadLength		= 0;
	I2CMasterBuffer[0] 	= MPU6050_ADDRESS;
	I2CMasterBuffer[1] 	= MPU6050_RA_GYRO_CONFIG;
	I2CMasterBuffer[2] 	= 0x08; // gyro range 600°/s

	state = I2CEngine();
	if(state != I2C_OK) return 1;

	I2CWriteLength 		= 3;
	I2CReadLength		= 0;
	I2CMasterBuffer[0] 	= MPU6050_ADDRESS;
	I2CMasterBuffer[1] 	= MPU6050_RA_ACCEL_CONFIG;
	I2CMasterBuffer[2] 	= 0x18; // 16G range

	state = I2CEngine();
	if(state != I2C_OK) return 1;

	return 0;
}

uint8_t MPU6050_whoami(){

	uint8_t state;

	I2CWriteLength 		= 2;
	I2CReadLength		= 1;
	I2CMasterBuffer[0] 	= MPU6050_ADDRESS;	  
	I2CMasterBuffer[1] 	= MPU6050_RA_WHO_AM_I;
	I2CMasterBuffer[2] 	= MPU6050_ADDRESS | RD_BIT;

	state = I2CEngine();
	if(state != I2C_OK) return state;

	if(I2CSlaveBuffer[0] != 0x68) return 1;

	return 0;
}

void MPU6050_setZero(){

	uint16_t i;
	uint16_t n = 1000;
	int32_t tmp_y= 0,tmp_x = 0, tmp_z = 0;
	int32_t ac_x=0, ac_y = 0, ac_z = 0;

	for(i=0;i<n;i++){
		tmp_y += MPU6050_getGyroRoll_raw();
	}
	for (i=0;i<n;i++){
		tmp_z += MPU6050_getGyroZ_raw();
	}
	for(i=0;i<n;i++){
		
		tmp_x += MPU6050_getGyroX_raw();
	}
	for (i=0;i<n;i++){
		ac_x += MPU6050_getAccel_x_raw();
	}
	for (i=0;i<n;i++){
		ac_y += MPU6050_getAccel_y_raw();
	}
	for (i=0;i<n;i++){
		ac_z += MPU6050_getAccel_z_raw();
	}
	tmp_y /= n;
	tmp_x /= n;
	tmp_z /= n;
	ac_y /= n;
	ac_x /= n;
	ac_z /= n;
	zero_gyro_roll = tmp_y;
	zero_X = tmp_x;
	zero_Z = tmp_z;
	zero_acc_x = ac_x;
	zero_acc_z = ac_z + 2048;
	zero_acc_y = ac_y;
	
}


int16_t MPU6050_getGyroRoll_raw(){

	int16_t tmp;
	uint8_t state;

	I2CWriteLength 		= 2;
	I2CReadLength		= 2; //1;
	I2CMasterBuffer[0] 	= MPU6050_ADDRESS;
	I2CMasterBuffer[1] 	= MPU6050_RA_GYRO_YOUT_H;
	I2CMasterBuffer[2] 	= MPU6050_ADDRESS | RD_BIT;

	state = I2CEngine();
	if(state != I2C_OK) return 1;

	tmp = (I2CSlaveBuffer[0]<<8) | I2CSlaveBuffer[1];
	//tmp = (I2CSlaveBuffer[0] << 8) ;

//	I2CWriteLength 		= 2;
//	I2CReadLength		= 1;
//	I2CMasterBuffer[0] 	= MPU6050_ADDRESS;
//	I2CMasterBuffer[1] 	= MPU6050_RA_GYRO_YOUT_L;
//	I2CMasterBuffer[2] 	= MPU6050_ADDRESS | RD_BIT;
//
//	state = I2CEngine();
//	if(state != I2C_OK) return 1;
//	tmp |= (I2CSlaveBuffer[0]) ;
	return tmp - zero_gyro_roll;
}

float MPU6050_getGyroRoll_degree(){

	int16_t tmp;
	float roll;

	tmp = MPU6050_getGyroRoll_raw();
	roll = (tmp / 65.536 );
	return roll;
}

float MPU6050_getGyroRoll_rad(){

	int16_t tmp;
	float roll;

	tmp = MPU6050_getGyroRoll_raw();
	roll = (float) ((tmp / 65.536) * 3.14159) / 180;
	return roll ;
}

int16_t MPU6050_getAccel_x_raw(){
	int16_t tmp;
	uint8_t state;

	I2CWriteLength 		= 2;
	I2CReadLength		= 2;   //1;
	I2CMasterBuffer[0] 	= MPU6050_ADDRESS;
	I2CMasterBuffer[1] 	= MPU6050_RA_ACCEL_XOUT_H;
	I2CMasterBuffer[2] 	= MPU6050_ADDRESS | RD_BIT;

	state = I2CEngine();
	if(state != I2C_OK) return 1;

    tmp = (I2CSlaveBuffer[0]<<8) | I2CSlaveBuffer[1];
//	tmp = (I2CSlaveBuffer[0] << 8) ;
//
//	I2CWriteLength 		= 2;
//	I2CReadLength		= 1;
//	I2CMasterBuffer[0] 	= MPU6050_ADDRESS;
//	I2CMasterBuffer[1] 	= MPU6050_RA_ACCEL_YOUT_L;
//	I2CMasterBuffer[2] 	= MPU6050_ADDRESS | RD_BIT;
//
//	state = I2CEngine();
//	if(state != I2C_OK) return 1;
//
//	tmp |= (I2CSlaveBuffer[0]) ;

	return tmp - zero_acc_x ;
}

float MPU6050_getAccel_x(){

	int16_t tmp;
	float x;

	tmp = MPU6050_getAccel_x_raw();
	x = (float) tmp / 2048;
	return x;
}

int16_t MPU6050_getAccel_z_raw(){

		int16_t tmp;
		uint8_t state;

		I2CWriteLength 		= 2;
		I2CReadLength		= 2;   //1;
		I2CMasterBuffer[0] 	= MPU6050_ADDRESS;
		I2CMasterBuffer[1] 	= MPU6050_RA_ACCEL_ZOUT_H;
		I2CMasterBuffer[2] 	= MPU6050_ADDRESS | RD_BIT;

		state = I2CEngine();
		if(state != I2C_OK) return 1;

		tmp = (I2CSlaveBuffer[0] << 8) | I2CSlaveBuffer[1];
//		tmp = (I2CSlaveBuffer[0] << 8) ;
//
//		I2CWriteLength 		= 2;
//		I2CReadLength		= 1;
//		I2CMasterBuffer[0] 	= MPU6050_ADDRESS;
//		I2CMasterBuffer[1] 	= MPU6050_RA_ACCEL_ZOUT_L;
//		I2CMasterBuffer[2] 	= MPU6050_ADDRESS | RD_BIT;
//
//		state = I2CEngine();
//		if(state != I2C_OK) return 1;
//
//		tmp |= (I2CSlaveBuffer[0]) ;
		return tmp - zero_acc_z; /* TBD */

}
float MPU6050_getAccel_z(){

	int16_t tmp;
	float z;

	tmp =  MPU6050_getAccel_z_raw() ;
	z = (float) tmp / 2048;
	return z;
}


int16_t MPU6050_getAccel_y_raw(){
	
	
		int16_t tmp;
		uint8_t state;

		I2CWriteLength 		= 2;
		I2CReadLength		= 2;   //1;
		I2CMasterBuffer[0] 	= MPU6050_ADDRESS;
		I2CMasterBuffer[1] 	= MPU6050_RA_ACCEL_YOUT_H;
		I2CMasterBuffer[2] 	= MPU6050_ADDRESS | RD_BIT;

		state = I2CEngine();
		if(state != I2C_OK) return 1;

		tmp = (I2CSlaveBuffer[0] << 8) | I2CSlaveBuffer[1];
	
	return tmp - zero_acc_y;
}

float MPU6050_getAccel_y(){
	
	int16_t tmp;
	float y;
	tmp = MPU6050_getAccel_y_raw();
	y = (float) tmp/2048;
	return y;
	
}

int16_t MPU6050_getGyroX_raw(void)
{
	int16_t tmp;
	uint8_t state;

	I2CWriteLength 		= 2;
	I2CReadLength		= 2; //1;
	I2CMasterBuffer[0] 	= MPU6050_ADDRESS;
	I2CMasterBuffer[1] 	= MPU6050_RA_GYRO_XOUT_H;
	I2CMasterBuffer[2] 	= MPU6050_ADDRESS | RD_BIT;

	state = I2CEngine();
	if(state != I2C_OK) return 1;

	tmp = (I2CSlaveBuffer[0]<<8) | I2CSlaveBuffer[1];

	return tmp - zero_X;
	
}
float MPU6050_getGyroX(void)
{
	int16_t tmp;
	float roll;

	tmp = MPU6050_getGyroX_raw();
	roll = (tmp  / 65.536 );
	return roll;
}

int16_t MPU6050_getGyroZ_raw(void)
{
	int16_t tmp;
	uint8_t state;

	I2CWriteLength 		= 2;
	I2CReadLength		= 2; //1;
	I2CMasterBuffer[0] 	= MPU6050_ADDRESS;
	I2CMasterBuffer[1] 	= MPU6050_RA_GYRO_ZOUT_H;
	I2CMasterBuffer[2] 	= MPU6050_ADDRESS | RD_BIT;

	state = I2CEngine();
	if(state != I2C_OK) return 1;

	tmp = (I2CSlaveBuffer[0]<<8) | I2CSlaveBuffer[1];

	return tmp - zero_Z;
	
}

float MPU6050_getGyroZ(void)
{
	int16_t tmp;
	float roll;

	tmp = MPU6050_getGyroZ_raw();
	roll = (tmp  / 65.536 );
	return roll;
}

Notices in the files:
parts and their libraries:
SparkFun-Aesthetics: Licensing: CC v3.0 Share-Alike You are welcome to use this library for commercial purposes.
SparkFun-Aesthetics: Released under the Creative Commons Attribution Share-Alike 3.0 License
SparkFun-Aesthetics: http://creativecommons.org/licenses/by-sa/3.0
